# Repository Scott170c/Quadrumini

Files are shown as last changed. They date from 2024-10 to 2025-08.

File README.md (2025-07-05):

# Quadrumini
### Affordable quadruped robot that can be modded with basic functionality! Updated models [HERE](https://github.com/Scott170c/Quadrumini/tree/main/inDev/QuadruminiV3)
```
Goals:
- Under $65 USD per unit
- Easy to assemble (be made into a kit?)
- Easy to modify
```
## Current Version: ` 3 `
<br></br>


Why I made this: <br>
After watching Boston Dynamics, I was always interested in quadrupedal robots (spot) and legged robots. I have seen many different quadrupedal robots both big and small, but a common factor between them is that they are all expensive. I wanted to make my own affordable (but high quality) version at home so I could learn how they worked and enjoy having one :)
<br></br>


BOM:
|Component |Description |Cost (USD)|Notes |Link |
|---|---|---|---|---|
|MG90S Servos |Small metal gear servo motor |29.99 |most cost efficient motor to use that wont snap when using |https://www.amazon.com/MG90S-Servo-Motor-Helicopter-Arduino/dp/B0CNL7Z2VY |
|Raspberry Pi Pico|Microcontroller |3.99 |For controlling the robot |https://www.microcenter.com/product/661033/raspberry-pi-pico-microcontroller-development-board |
|2S Lipo Battery  |Lipo Battery 1000mah |8.99 |Lightweight, around 60g |https://www.amazon.com/Gens-ace-1000mAh-Helicopter-Airplane/dp/B012CMFAL2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|
|UBEC |Universial Battery Eliminator Circuit|3.15 |to step down voltage to safe operating voltage for components|https://www.aliexpress.us/item/2255799846479441.html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|
|PCB |For driving the the motors, computing|80.79 |not needed for now, will prob use stray components |LCSC |
|MPU6050 |for Gyro/Accel |1.86 |Not needed, can be added for extra sensing |https://www.aliexpress.us/item/3256809057355938.html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|
Total: | $126.91 USD |

Handwire (I will be following this):
|Component |Description |Cost (USD)|Notes |Link |
|---|---|---|---|---|
|MG90S Servos |Small MG (metal gear) servo |$29.99 |Smallest motor w/ metal gears for added strength|https://www.amazon.com/MG90S-Servo-Motor-Helicopter-Arduino/dp/B0CNL7Z2VY|
|Raspberry Pi Pico |MCU to control the robot (the brain) |$3.99 |For controlling the robot |https://www.microcenter.com/product/661033/raspberry-pi-pico-microcontroller-development-board|
|2S Lipo Battery |Lipo Battery (1000 mah , 7V) |$8.99 |Lightweight, around 60g |https://www.amazon.com/Gens-ace-1000mAh-Helicopter-Airplane/dp/B012CMFAL2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|
|UBEC |Battery eliminator circuit |$3.15 |Needed to step down voltage from 7V to 5V |https://www.aliexpress.us/item/2255799846479441.html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|
|PCA9685 Servo Driver |Drives servos through I2C |$3.34 |Needed to drive all of the servos |https://www.aliexpress.us/item/3256808284749606.html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|
|MPU6050 |For sensing Gyro/Accel |$1.86 |Not needed, can be added for extra functionality|https://www.aliexpress.us/item/3256809057355938.html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|
|Logic-Level Converter|shifting logic from 5V to 3V3 for PCA module|$2.41 |Needed to shift to lower voltage logic |https://www.aliexpress.us/item/3256808042987546.html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|
Total: | $53.73 USD |

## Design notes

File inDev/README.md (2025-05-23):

# Quadrumini Devlog
`April 27, 2024`: I decided to make a devlog to motivate me to work on Quadrumini consistently. I made a test gait back in early march but my laptop is currently being repaired so no code yet.
___
`October 24, 2024`: I guess the devlog did not motivate to work on Quadrumini consistently lol. My scheduled has freed up so I started working on redesigning the CAD for version 2 <br /> <br />
changes:
- new legs (lighter, smaller, easier to work with)
- progress on the body
- planning for a design with 3 DOF (per leg), but a baseline 2 DOF for a basic version
___
`May 22, 2025`: Finally had time to get things printed and tested, the V2 works well albeit hard to set up (servo zeroing). It currently runs on 8 mg90 servos, an arduino nano, servo driver module, and 9V battery! Some small program tests I've ran have been pretty successful and it is able to carry it's own weight :) <br /> <br />
I think this is the end for the V2, and I will be starting a V3 for highway to undercity, where the 3 DOF per leg + PCB will be made (and lots of design changes to the body!)

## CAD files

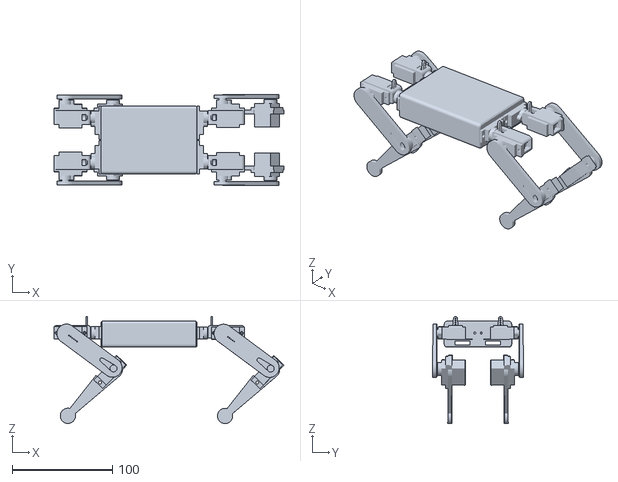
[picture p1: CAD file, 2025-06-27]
inDev/QuadruminiV3/Full CAD.stl
229.5 x 90.7 x 107.0

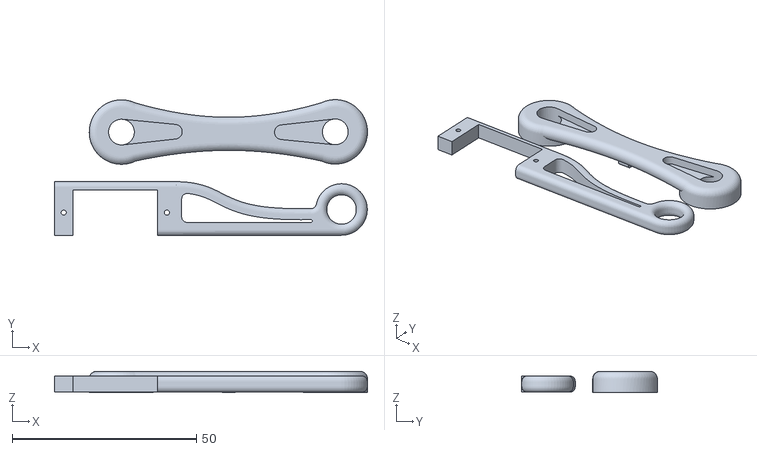
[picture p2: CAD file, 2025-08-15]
inDev/QuadruminiV3/Final Leg 3DP.stl
85.0 x 36.9 x 5.81

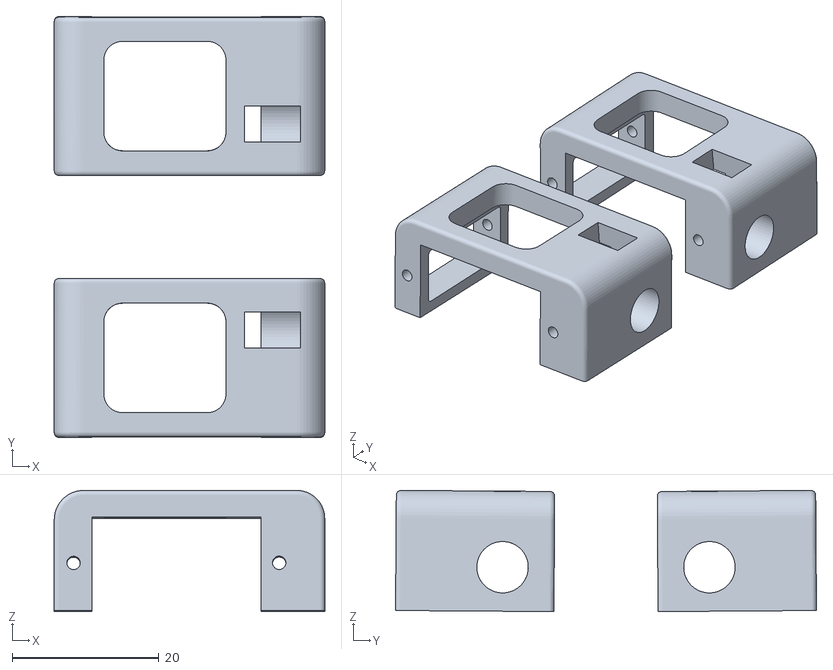
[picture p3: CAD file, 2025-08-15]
inDev/QuadruminiV3/Final Rotator Cuff 3DP.stl
36.8 x 57.3 x 16.5

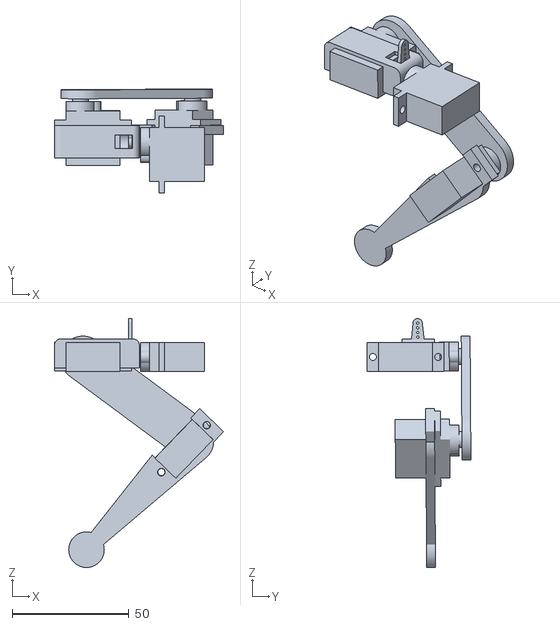
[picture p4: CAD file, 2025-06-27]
inDev/QuadruminiV3/Final Leg CAD.stl
72.5 x 44.5 x 106.7

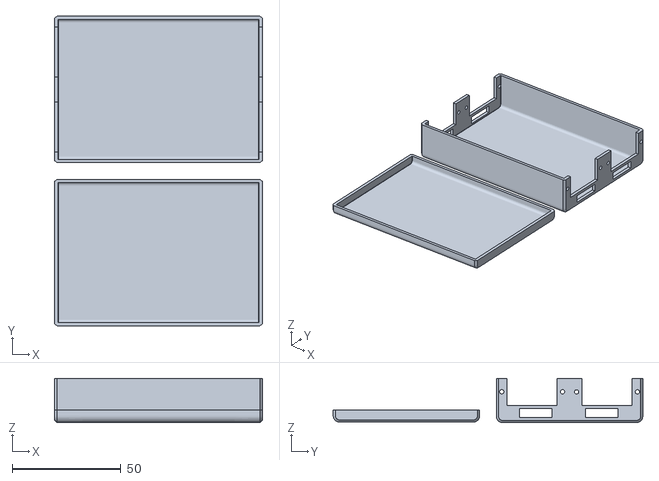
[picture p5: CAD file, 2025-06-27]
inDev/QuadruminiV3/Final Body 3DP.stl
95.6 x 142.4 x 20.4

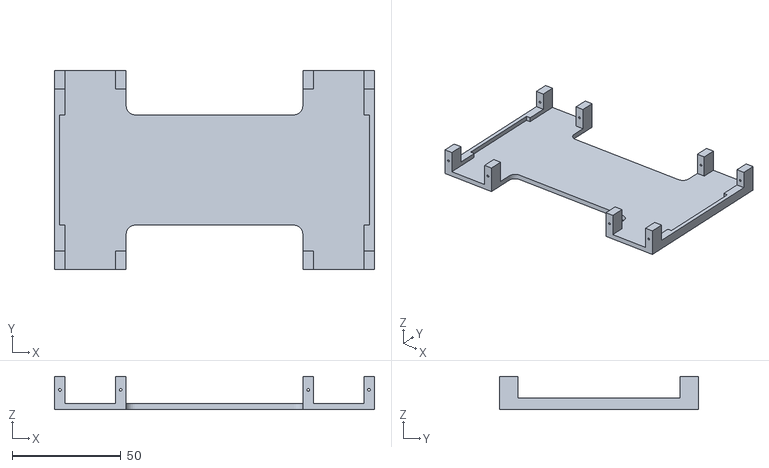
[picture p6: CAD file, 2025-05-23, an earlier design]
inDev/QuadruminiV2/bodyV2.stl
147.3 x 91.4 x 15.2

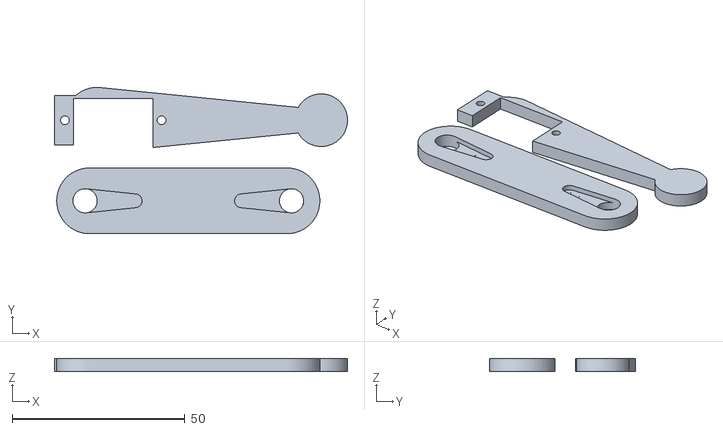
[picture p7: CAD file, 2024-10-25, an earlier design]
inDev/QuadruminiV2/Quadruped Leg.stl
84.8 x 42.4 x 3.82

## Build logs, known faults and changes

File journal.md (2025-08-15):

---
title: "Quadrumini"
author: "@Scott"
description: "Small and affordable quadruped robot"
created_at: "2025-06-05"
---

### Quadrumini Journal started for [Highway to Undercity](https://highway.hackclub.com/)
total hours worked: `27`

# `6/3/2025` - Research on Electronics Design (1 hr)
I did some calculations for the power source I need in order to power my quadruped, and I have come up with two options:
- Stay with 8 motors and have 4 DOF
- Upgrade to 12 motors and have all 6 DOF
I think I will be ambitious, and go for the 12 motors to have all 6 DOF, but the power consuption will be really high 👀

Also did research on motors, and I will be sticking with the MG90! I want to keep my robot affordable 🥳

# `6/4/2025` - Research on General Design (1.5 hrs)
Today, I did some research on different types of legs, and since one of my goals is to have my robot jump I was thinking of using a compliant leg. I looked into many designs and if I do end up going for a compliant leg I will most likely be going with this one! I like it's simplicity.

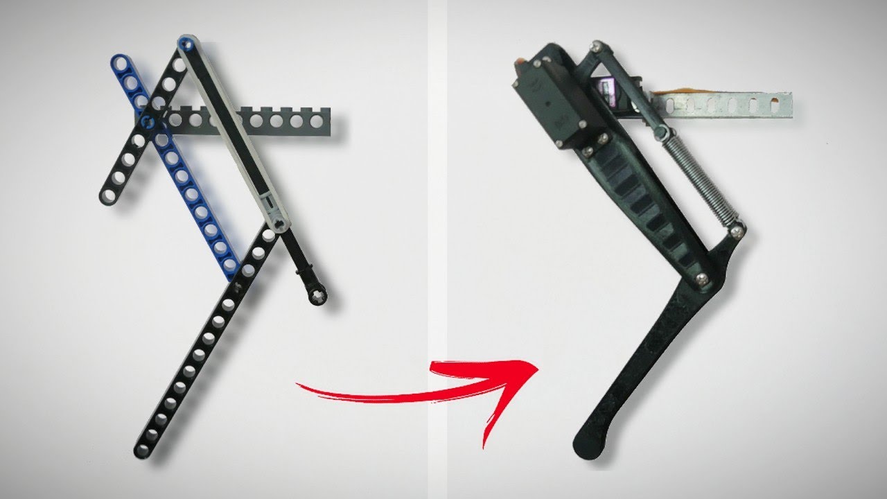
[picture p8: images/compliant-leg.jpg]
 

[Design by Adam Beedle](https://www.youtube.com/watch?v=bDxItdyQ3jc)

On Saturday, I hope to start working on my first CAD and print out a couple iterations :)

# `6/10/2025` - More Research & CAD (3.5 hrs)
I looked into which MCUs to use and came to the conclusion that the Raspberry Pi Pico would be the best option for me, coupled with a PCA9685 Servo Driver. It is able to give me the power I need to move all 12 servos at once and keep it cost efficient :) It's power will be a massive upgrade from the Arduino Nano I have been testing with.

<br></br>
I also started cading the leg for the robot, and got some progress. A lil rusty with Fusion 360 so it took me longer than I would like to admit (which is why I spent so much time here) but I got the CAD done and learned how to put articulate joints on! Each leg has 3 DOF!
<br></br>
 
<br></br>
Because there is now 3 DOF per leg, I have decided to not design a compliant leg. I may design one in the future but I have decided to go for more degrees of freedom 🕺 over jumping ⬆️ for now.

# `6/14/2025` - Hip Flexor Design + Start on PCB (4 hrs)
Today, I got a lot done! I remade the CAD for the hip flexor to shed some weight and also make it easier to use, and started working on the PCB for the robot, which I intend to use to drive the entire thing off of!
<br>
Hip Flexor Redesign:
<br></br>
 
<br></br>
The last design was very boxy, and took up a lot of space laterally, which was limited. With this redesign, I moved it's bracing to be vertical and made it overall thinner! It is also now way easier to put in the servo horn :)
<br>
Current PCB Schematic:
<br></br>
 
<br></br>
I am using the Raspberry Pi Pico as my MCU (Microcontroller Unit) and will be using the PCA9685 chip to drive everything, which makes it so that I can drive all of the servos through one I2C connection! I decided to put everything on a PCB, as I wanted to minimize the amount of wires as much as possible. This design option will give me more space in the housing to cram the servo wires in, and put my MPU chip in a more precise spot! (will be implementing that very soon)

# `4/15/2025` - Tons of CAD (5 hrs)
Spent a lot of time today on CAD, went through multiple iterations of design for the housing. Unfortunately I forgot to take progress pictures, but this is what I finally came up with:
<br></br>
 
<br></br>
I felt the design was nice, but I realized that because of the way my leg is designed the front legs are unable to bend fully (as seen in the picture above)
<br>
So anyway, heres what needs to be done left:
- finalize PCB + circuit
- re-design housing (?)

Hopefully I will be able to get it done soon!

# `4/20/2025 - 4/25/2025` - Finalized Design (12 hrs)
I haven't been journaling consistently due to summer classes kicking up (oops) but I have been working here and there over the past week. Lots of progress! Here is the finished schematic of the PCB + 3D render!
<br></br>
 
 
 
<br></br>
For the actual connections, the way it will work is I will have a 2S Lipo battery connected to a UBEC (Universial Battery Eliminator Circuit) which will then feed into the PCB. The motors then get connected to the PCB to be controlled :)
Basically, it goes `2S Lipo` -> `UBEC` -> `PCB` -> `Servos`
<br>
For more accurate control, I also added in a MPU module that can be stuck on the bottom of the PCB! This concludes the design part of the journal, and hopefully the next portion will be me building it out :)

# `4/26/2025` - Final CAD + Attempts of adding PCB Model (2 hrs)
Final CAD! YIPPE!
<br></br>

<br></br>
Unfortunately, because I designed in EasyEDA it is goofy hard to try to export my pcb as a 3d model, so I will leave that problem for tomorrow me but I know it fits so :)

# `8/14/2025` - Testing out circuit (3 hrs)
So today I recieved all of my parts! I only have a bit of 3D printed parts left before I can assemble the whole thing so I decided to test if my circuitry would work.

I blew up my last PCA9685 Servo Driver unfortunately, so I had to improvise and make a testing board with a orpheus pico (pi pico clone) lying around... when I turned it on and boosted my test program, things did not go as expected. The servos were extremely underpowered, and only half of them were able to be controlled. I'm deciding to wait until the PCA module I ordered comes in the mail and hoping it works.

# `8/9/2025` - Full Build (6 hrs)
I finally got the PCA board and finished 3D printing everything, so I've started assembling it today! Everything is looking great right now except for the fact that the wires stick out too much, so I wont be able to put a lid on the housing :( 

Here is what it looks like fully built out!
<br></br>


# 8/10/2025 - Coding (6 hrs)
I started coding little commands for it to do, it is able to twist and dance around but not able to fully walk just yet. I've been walking some youtube videos on how other people approach making their robots walk. 

Here is a [demo video](https://youtu.be/tfDZpeDsz_g) of it moving!

# `0/0/2025` - Title (_ hrs)

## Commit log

2024-10-25 Rename Quadruped Leg.stl to Quadruped Leg.stl
    [Quadruped Leg.stl]
2025-05-23 Add body stl to V2
    [bodyV2.stl]
2025-06-27 add V3 STLs (for highway)
    [Body CAD v7.stl, Full CAD v7.stl, Full Leg CAD v16.stl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]
2025-07-01 Update BOM - handwire.csv
    [BOM - handwire.csv]
2025-08-15 add final designs
    [Leg but Thicker.stl, Rotator Cuff Final.stl]
2025-08-15 Rename Body CAD v7.stl to Final Body.stl
    [Final Body.stl]
2025-08-15 Rename Full CAD v7.stl to Full CAD.stl
    [Full CAD.stl]
2025-08-15 Rename Full Leg CAD v16.stl to Final Leg CAD.stl
    [Final Leg CAD.stl]
2025-08-15 Rename Leg but Thicker.stl to Final Leg 3DP.stl
    [Final Leg 3DP.stl]
2025-08-15 Rename Final Body.stl to Final Body 3DP.stl
    [Final Body 3DP.stl]
2025-08-15 Rename Rotator Cuff Final.stl to Final Rotator Cuff 3DP.stl
    [Final Rotator Cuff 3DP.stl]
